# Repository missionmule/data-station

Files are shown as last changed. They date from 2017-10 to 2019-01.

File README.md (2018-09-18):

# Data Station

This repository holds all information necessary to build a Mission Mule Data Station.

## Raspberry Pi Software

## Hardware (~$295)
### Ordering the PCB
1. Download both zip folders in the latest version of fabrication files folder.
2. Upload them to [Seeed Studio Fusion PCB Manufacturing](https://www.seeedstudio.com/fusion_pcb.html).
3. Make the following selections:
    1. Base Material: FR4 TG130
    2. No. of Layers: 2
    3. PCB Dimensions: 155mm x 80mm
    4. PCB Quantity: whatever you want
    5. No. of Different Designs: 1
    6. PCB Thickness: 1.60 mm
    7. PCB Color: Green
    8. Surface Finish: HASL
    9. Minimum Solder Mask Dam: 0.4mm
    10. Copper Weight: 1oz.
    11. Minimum Drill Hole Size: 0.3mm
    12. Trace Width / Spacing: 6/6 mil
    13. Blind or Buried Vias: No
    14. Plated Half-holes / Castellated Holes: No
    15. Impedance Control: No
    
**Estimated Cost: $6.90**

### Ordering the Components

Items in BOM 1  are less ubiquotous and should be ordered on a per data station basis. Items in BOM 2 often arrive in bulk, so order accordingly. Items in BOM 3 should be ordered on a per PMC basis. 

BOM 1 - Enclosure - DigiKey Components - [Octopart Link](https://octopart.com/bom-tool/w3m3v7al)

| Item | Qty | Part Number | Unit Price  | Line Total  | 
|---|-----|---|---|---|
| Bud Industries Enclosure | 1 | PTS-25319-C | 17.46 | 17.46 | 
| 3D Printed Base Plate | 1 | 3mm PLA Base Plate | 0.00 | 0.000 | 
| Voltaic V44 battery, 12,000 mAh USB LiPo  | 1 | V44 Voltaic Battery | 69.00 | 69.00 | 
| Voltaic 9W Solar Panel | 1 | 9W Voltaic Solar Panel | 79.00 | 79.00 | 
| Bulkhead, USB A to USB B | 1 | PX0842/A | 11.12 | 11.12 | 
| Bulkhead, USB Mini to unterminated wires, | 1 | PX0457 | 7.93 | 7.93 | 
| Sealed Cable, USB A to USB Mini | 1 | PX0441/2M00 | 16.58 | 16.58 |
| XBee Antenna | 1 | 001-0002 | 13.61 | 13.61 | 
| Bulkhead Pass-through, Xbee Antenna | 1 | AIO-CSPG16 | 2.23 | 2.23 | 
| WiFi Antenna | 1 | ICEFINLDMN | 46.52 | 46.52 | 
| Cable, USB A to USB B, 30cm | 1 | 321010003 | 1.70 | 1.70 |

**Estimated Total Cost: $110.15**

BOM 2 - Enclosure - Other Components

| Item | Qty | Unit Price | Line Total | Link | 
|---|-----|---|---|---|
|M4 Standoffs| 4 | 0.894 | 3.576 | [Amazon](https://www.amazon.com/gp/product/B0177VG4Q8/ref=oh_aui_detailpage_o09_s00?ie=UTF8&psc=1) |
|M4 Screws | 8 | 0.04 | 0.30 | [Amazon](https://www.amazon.com/gp/product/B07DF7GVRB/ref=oh_aui_detailpage_o09_s00?ie=UTF8&psc=1) |
|90mm RP-SMA extension| 1 | 3.50 | 3.50 | [Amazon](https://www.amazon.com/gp/product/B076TCPTKL/ref=oh_aui_detailpage_o05_s00?ie=UTF8&psc=1) |
|30 cm RP-SMA extension | 1 | 4.00 | 4.00 | [Amazon](https://www.amazon.com/Male-Female-Antenna-Extension-Cable/dp/B072VMHXSQ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) |
|Male Headers  | ~10 | ~0.10 | ~1.00 | [Amazon](https://www.amazon.com/Hotop-Pack-Single-Header-Connector/dp/B06XR8CV8P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) |
|Female Headers| ~10 | ~0.10 | ~1.00 | [Amazon](https://www.amazon.com/2-54mm-Straight-Connector-Assortment-Arduino/dp/B0785SP8PB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)|
|Raspi Female Headers| 1 | ~0.60 | ~0.60 | [Amazon](https://www.amazon.com/uxcell-2-54mm-40-Pin-Female-Connector/dp/B00R1LLM1M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) |
|Raspi Male Header | 1 | ~0.80 | ~0.80 | [Amazon](https://www.amazon.com/s?url=search-alias%3Daps&field-keywords=2x20+male+header) |

**Estimated Total Cost: $11.38**

BOM 3 - Power Management Circuit - [Octopart Link](https://octopart.com/bom-tool/1G1U2eW2#)

| Description | Qty | Line Item | Unit Price | Line Total | 
|---|-----|---|---|---|
| GPS Module | 1 | 746 | 34.95 | 34.95 | 
| Raspberry Pi 0W | 1 | ADA3400 | 10 | 10.00 | 
| Arduino Pro Mini | 1 | 2378 | 9.95 | 9.95 | 
| Voltage Regulator | 1 | POLOLU-2118 | 4.97 | 4.97 | 
| FET Switch | 2 | POLOLU-2808 | 4.5 | 9.00 | 
| XBee Explorer | 1 | WRL-11373 | 9.95 | 9.95 | 
| XBee Pro S3B | 1 | 602-1349-ND | 37.97 | 37.97 | 
| Logic Converter | 1 | BOB-12009 | 2.003 | 2.00 | 
| Reed Switches | 4 | 59165-1-S-00-A | 0.715 | 2.86 | 
| LEDs | 4 | 204-10SURD/S530-A3 | 0.0619 | 0.25 | 
| Opto Isolator | 1 | LTV-816 | 0.077 | 0.08 | 
| 1K Resistors | 4 | CF14JT1K00 | 0.01 | 0.04 | 
| 2.1K Resistor | 3 | RNF14FTE2K10 | 0.39 | 1.17 | 
| Temp/Humidity Sensor | 1 | HIH8120-021-001 | 5.38 | 5.38 | 
| USB Micro Breakout | 1 | 1833 | 1.5 | 1.50 | 
| Debug Switches | 6 | [link](https://www.amazon.com/gp/product/B06XJN3K8K/ref=oh_aui_detailpage_o03_s00?ie=UTF8&psc=1) | 0.15 | 0.91 |
| USB Hub | 1 | [link](https://www.amazon.com/MakerSpot-Stackable-Raspberry-Connector-Bluetooth/dp/B01IT1TLFQ) | 13.99 | 13.99 |
| Wifi Module | 1 | [link](https://www.amazon.com/gp/product/B00YI0AIRS/ref=oh_aui_detailpage_o03_s00?ie=UTF8&psc=1) | 18.99 | 18.99 |

**Estimated Total Cost: $163.95**

### Assembly
#### Power Management Circuit
Right now, the PMC is made with through hole components. Seeed Studio manufactures the PCB, and Mission Mule separately buys and solders all of the electronic components. For max eficiency, remove regulator and led on the Arduino Pro Mini (easily done with a small knife or pliers).

IMPORTANT: The XBee Pro S3B [does not work with loads connected to the RSSI signal](https://www.sparkfun.com/products/11634). Thus, the RSSI pin on the XBee explorer must be removed. Additionally, remove the RSSI LED on the explorer (easily done with a small knife or pliers). 

#### Enclosure
assemble and stuff...

## Power Management Firmware
### Requirements
1. Arduino IDE
2. [Adafruit GPS Arduino Library](https://github.com/adafruit/Adafruit_GPS)

Download the code in the [DataStation](https://github.com/missionmule/data-station/tree/master/Microcontroller) and compile for "Arduino Pro or Pro Mini". Upload  using an [FTDI Basic Breakout Board](https://www.sparkfun.com/products/9716).

### XBee Module
Download [XCTU](https://www.digi.com/products/xbee-rf-solutions/xctu-software/xctu) in order to configure the XBee module:
* ID: 1005
* HP: 1
* DT: 10
* MY: 20
* BD: 57600

### Voltaic Battery
The Voltaic battery must be configured for "Always On Mode". Follow the [Voltaic Guide](https://www.voltaicsystems.com/always-on#faq_4) to determine its current mode and to switch it into the approproate mode.

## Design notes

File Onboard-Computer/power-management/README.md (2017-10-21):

## Raspberry Pi
This code runs on the Raspberry Pi to backup photos. This code is currently
not used.

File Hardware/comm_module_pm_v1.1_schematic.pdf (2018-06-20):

# Power Supplies

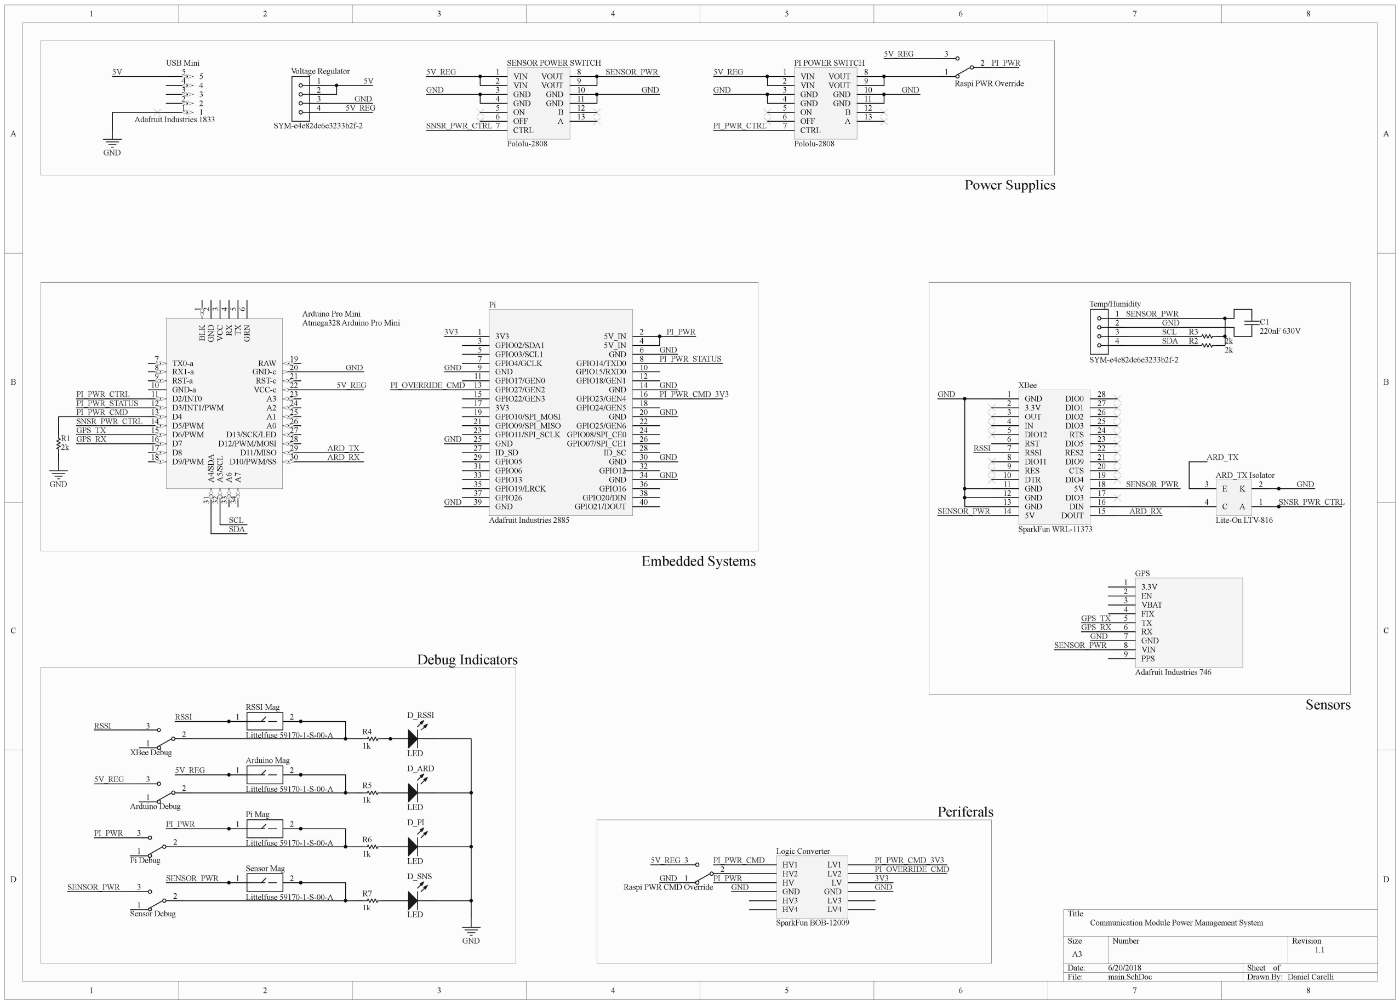
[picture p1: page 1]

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
Title

Size | Number | Revision
A3
Date: | 6/20/2018 | Sheet of
File: | main.SchDoc | Drawn By:

GND

Communication Module Power Management System

Daniel Carelli

1.1

GND 1
3.3V 2
OUT 3
IN 4
DIO12 5
RST 6
RSSI 7
DIO11 8
RES 9
DTR 10
GND 11
GND 12
GND 13
5V 14 | DOUT | 15 DIN | 16 DIO3 | 17 5V | 18 DIO4 | 19 CTS | 20 DIO9 | 21 RES2 | 22 DIO5 | 23 RTS | 24 DIO3 | 25 DIO2 | 26 DIO1 | 27 DIO0 | 28

XBee

SparkFun WRL-11373

GND

ARD_RX

1
2
3
4

Temp/Humidity

SYM-e4e82de6e3233b2f-2

SENSOR_PWR
GND | C1
SCL | 220nF 630V
SDA

R3
R2 | 2k
| 2k

1
2
3
4

Voltage Regulator

SYM-e4e82de6e3233b2f-2

5V

5V_REG

GND

1

2

3

Raspi PWR Override

R5
1k

D_ARD

LED

R6
1k

D_PI

LED

R7
1k

D_SNS

LED

PI_PWR

1

2

3

Arduino Debug

1

2

3

Pi Debug

1

2

3

Sensor Debug

GND

SENSOR_PWR

PI_PWR

5V_REG

VIN 1
VIN 2
GND 3
GND 4
ON 5
OFF 6
CTRL 7
VOUT | 8
VOUT | 9
GND | 10
GND | 11
B | 12
A | 13

PI POWER SWITCH

Pololu-2808

PI_PWR

GND

5V_REG

GND

PI_PWR_CTRL

VIN 1
VIN 2
GND 3
GND 4
ON 5
OFF 6
CTRL 7
VOUT | 8
VOUT | 9
GND | 10
GND | 11
B | 12
A | 13

SENSOR POWER SWITCH

Pololu-2808

SENSOR_PWR

GND

5V_REG

GND

5V_REG

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
Logic Converter

SparkFun BOB-12009

3V3 1

| 5V_IN | 2
5V_IN | 4 GPIO02/SDA1 3
GPIO03/SCL1 5 | GND | 6
GPIO4/GCLK 7 | GPIO14/TXD0 | 8
GND 9 | GPIO15/RXD0 | 10
GPIO17/GEN0 11
GPIO27/GEN2 13
GPIO22/GEN3 15
3V3 17
GPIO10/SPI_MOSI 19
GPIO09/SPI_MISO 21
GPIO11/SPI_SCLK 23
GND 25
ID_SD 27 | ID_SC | 28
GPIO05 29
GPIO06 31
GPIO13 33
GPIO19/LRCK 35
GPIO26 37
GND 39 | GPIO21/DOUT | 40 GPIO20/DIN | 38 GPIO16 | 36 GND | 34 GPIO12 | 32 GND | 30
GPIO07/SPI_CE1 | 26 GPIO08/SPI_CE0 | 24 GPIO25/GEN6 | 22 GND | 20 GPIO24/GEN5 | 18 GPIO23/GEN4 | 16 GND | 14 GPIO18/GEN1 | 12

Pi

Adafruit Industries 2885

PI_PWR

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
GND | GND

PI_PWR

PI_PWR_STATUS

PI_OVERRIDE_CMD

PI_PWR_CMD

3V3

3V3

PI_PWR_CMD_3V3

PI_PWR_CMD_3V3

PI_OVERRIDE_CMD

1

2

3

Raspi PWR CMD Override

GND

5V_REG

5V_REG

R4
1k

D_RSSI

LED

1

2

3

XBee Debug

RSSI
RSSI

RSSI

SENSOR_PWR

SENSOR_PWR

# Embedded Systems

# Sensors

# Periferals

# Debug Indicators

A

1

K

### 2 E

3

C

4

ARD_TX Isolator

Lite-On LTV-816

GND

ARD_TX

3.3V 1
EN 2
VBAT 3
FIX 4
TX 5
RX 6
GND 7
VIN 8
PPS 9

GPS

Adafruit Industries 746

GPS_TX
GPS_RX

SENSOR_PWR

GND RX

4

VCC-c 22
D2/INT0 11
D3/INT1/PWM 12
D4 13
D5/PWM 14
D6/PWM 15
D7 16
D8 17
D9/PWM 18 | D10/PWM/SS | 30 D11/MISO | 29 D12/PWM/MOSI | 28 D13/SCK/LED | 27 A0 | 26 A1 | 25 A2 | 24 A3 | 23 A⁶ 33 A⁷ 34 BLK

1

GND-a 10 | TX

### 5 GRN

6

GND-c | 20 RAW | 19
RST-a 9 | RST-c | 21 RX1-a 8 | VCC

3

TX0-a 7 | GND

# 2 A4/SDA 31 A5/SCL 32

Arduino Pro Mini
Atmega328 Arduino Pro Mini

5V_REG

GND

ARD_RX

ARD_TX

PI_PWR_CTRL
PI_PWR_STATUS

SNSR_PWR_CTRL

PI_PWR_CMD

R1
2k

GND

SCL
SDA

SNSR_PWR_CTRL

GPS_TX
GPS_RX

1 2

RSSI Mag

Littelfuse 59170-1-S-00-A

1 2

Arduino Mag

Littelfuse 59170-1-S-00-A

1 2

Pi Mag

Littelfuse 59170-1-S-00-A

1 2

Sensor Mag

Littelfuse 59170-1-S-00-A

SENSOR_PWR

SNSR_PWR_CTRL

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
USB Mini

Adafruit Industries 1833

5V

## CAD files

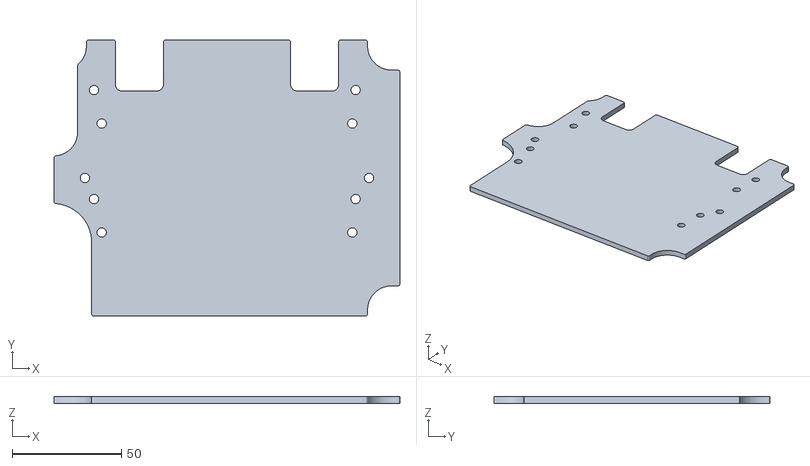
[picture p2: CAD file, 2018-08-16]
Hardware/base_plate_3mm.stl
158.7 x 126.7 x 3.00

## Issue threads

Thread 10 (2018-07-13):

add timeout to shutdown procedure

dbcarelli, 2018-07-13:
When cutting power to the RPi, the Arduino monitors the TX line of the Pi to determine when it is off before cutting power. This functionality should have a timeout i.e. if the Pi doesn't shutdown in 5 mins, power will be cut regardless.

dbcarelli, 2018-07-14:
[commit 84513ff](https://github.com/missionmule/data-station/commit/f7ffd9e1f4ddba3d3ad07a96338301c03a6d0fc2)

Closed 2018-07-14.

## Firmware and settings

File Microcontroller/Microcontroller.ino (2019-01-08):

#include "Communication.h"
#include "PowerManager.h"
#include "SensorComm.h"

int shutdownStart = 1;

char STATION_ID[3] = {'1', '0', '1'};

volatile int f_wdt=1;
volatile int count = 0;

Communication * comms = new Communication(10, 11, 57600, STATION_ID); // RX, TX, Baudrate
PowerManager * powerManager = new PowerManager(comms, &f_wdt);
SensorComm * sensorComm = new SensorComm();

char droneCommand;

unsigned long timerStart;
unsigned long timeElapsed;
const unsigned long TIMEOUT = 6000000;

void executeCommand(char command) {
  char startDelimiter = '~';
  String packetOut;

  comms->write(startDelimiter);

  comms->write(STATION_ID[0]);
  comms->write(STATION_ID[1]);
  comms->write(STATION_ID[2]);

  comms->write(command);

  // flush outgoing and incoming buffer, respectively
  comms->flush();
  //comms->flushIncommingBuffer();

  // execute the requested command
  switch (command) {
    case '1':
      Serial.println("Received Command: POWER_ON");
      shutdownStart = 0;
      powerManager->powerUpSystem();
      break;

    case '2':
      Serial.println("Received Command: POWER_OFF");
      shutdownStart = 1;
      break;

    case '3':
      Serial.println("Received Command: EXTEND_TIME");
      timerStart = millis();
      break;

    case '4':
      Serial.println("Received Command: RESET_ID");
      if (comms->getNewId()){
        STATION_ID[0] = comms->getId(0);
        STATION_ID[1] = comms->getId(1);
        STATION_ID[2] = comms->getId(2);
        Serial.print("New ID set: ");
        Serial.print(STATION_ID[0]);
        Serial.print(STATION_ID[1]);
        Serial.println(STATION_ID[2]);
      }
      break;

    case '5':
      Serial.println("Received Command: REQUEST_GPS");
      sensorComm->begin();
      sensorComm->listen();
      packetOut = sensorComm->getGpsData();
      comms->listen();
      // send prelimitor, GPS Data, then postlimitor
      comms->write('<');
      comms->writeString(packetOut);
      comms->write('>');
      break;

    case '6':
      Serial.println("Received Command: DEPLOYMENT_SYS_TEST");
      comms->write('<');
      comms->writeString("245233230,544344570");
      comms->write('>');
      break;

    default:
      Serial.println("ERROR: Command not recognized");
      break;
  }

}

// TODO: Add support for UBlox GPS Module, comm with I2C

void setup(){
  Serial.begin(57600);
  sensorComm->begin();
  comms->begin();
  comms->listen();

  // Initialize Watchdog Timer
  powerManager->setupWatchDogTimer();

  Serial.println("Initialized");
}

// Watchdog Interrupt Service. This is executed when watchdog timed out.
ISR(WDT_vect) {
  if(f_wdt == 0) {
    if (count >= 4){
      count = 0;
      f_wdt=1;
    }
    else{
      count++;
    }
  }
}

void loop(){
  // Wait until the watchdog has triggered a wake up.
  if(f_wdt != 1) {
    powerManager->enterSleep();
    return;
  }

  Serial.println("Awake!");

  droneCommand = comms->getDroneCommand();

  if (droneCommand){
    timerStart = millis();
    Serial.println("Drone in vicinity...");
    executeCommand(droneCommand);

    while (!shutdownStart){
      timeElapsed = millis()-timerStart;
      Serial.print("Time remaining (seconds): ");
      Serial.println((TIMEOUT-timeElapsed)/1000);

      if (timeElapsed > TIMEOUT){
        Serial.println("Timeout event...");
        break;
      }

      droneCommand = comms->getDroneCommand();

      if (droneCommand)
        executeCommand(droneCommand);

      delay(200);

    }
  }
  else{
      Serial.println("No messages received");
  }

  Serial.println("Going to slepp...ZZzzz");
  powerManager->shutDownSystem();

 }

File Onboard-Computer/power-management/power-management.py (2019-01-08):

import logging
import os
import sys
import time

import RPi.GPIO as GPIO

# Log to STDOUT
ch = logging.StreamHandler(sys.stdout)
ch.setLevel(logging.INFO)
formatter = logging.Formatter('%(asctime)s.%(msecs)03d %(levelname)s %(message)s')
ch.setFormatter(formatter)
logging.getLogger().addHandler(ch)

# Map pins to P1 header on the Raspberry Pi
GPIO.setmode(GPIO.BOARD)

# Power Status of the RPi, as observed by the Arduino
pi_power_status = 8

# Manual override of power-off command
pi_override_cmd = 13

# Arduino-command to power-off RPi
pi_power_cmd_3v3 = 16

# Setup
GPIO.setup(pi_power_status, GPIO.OUT)
GPIO.setup(pi_override_cmd, GPIO.IN)
GPIO.setup(pi_power_cmd_3v3, GPIO.IN)

# Always set HIGH. When RPi is powered, the arduino knows through this signal.
GPIO.output(pi_power_status, GPIO.HIGH)

while True:
    time.sleep(5)
    if (GPIO.input(pi_override_cmd) or GPIO.input(pi_power_cmd_3v3)):
        if (GPIO.input(pi_override_cmd)):
            logging.debug("PI_OVERRIDE_CMD is HIGH")
        else:
            logging.debug("PI_POWER_CMD_3V3 is HIGH")
    else:
        # There is no cmd intructing to RPi to be on. Make sure this is true
        # in 5 seconds.
        logging.info("Initiating shutdown...")
        time.sleep(5)
        if not (GPIO.input(pi_override_cmd) or GPIO.input(pi_power_cmd_3v3)):
            logging.info("Shutting down")
            os.system("sudo shutdown now")
        else:
            logging.info("Aborting shutdown")

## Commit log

2018-02-01 Adding code to control new Power Management Circuit
2018-04-02 Create prototype function for PowerManager class. Romove power management logic from main.
2018-04-03 Write in logic for PowerManagement class.
2018-04-04 Add skeleton code for reading in new ID and returning sensor data
2018-04-05 Add SensorComm header file + support in other files.
2018-06-20 Add fabrication files for the power management circuit v1.1
2018-06-20 Change Electronics folder to Hardware. Add BOM.
    [bill_of_materials.xlsx]
2018-06-20 Add PMC schematic.
2018-07-12 Connect XBee ground to the ground
2018-07-13 Add power status script
2018-07-14 Add power-off timeout
2018-08-16 Add STL for data station baseplate, for 3D printing.
    [base_plate_3mm.stl]
2018-08-16 Remove BOM spreadsheet
    [bill_of_materials.xlsx]
